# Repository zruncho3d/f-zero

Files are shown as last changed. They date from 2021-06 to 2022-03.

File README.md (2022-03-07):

# F-Zero - an Evolved Voron Zero

by Zruncho and `#flying-zero` collaborators on the [DoomCube Discord](https://discord.gg/doomcube):
L.e.o.p.a.r.d, finn, Kayos Maker, hartk, ericsson, sci, and more.

**Upgrade your V0 or build a fresh F0.**

**Full auto-calibration at a fraction of the price of a V2.**

**Make every first layer perfect!**

### → [See one in action!](https://youtu.be/jLSPeJ7L9R4)  (V0.802 Serial Request)
### → [See CAD in your browser!](https://grabcad.com/library/f-zero-cad-1)
### → [Parts List!](https://docs.google.com/spreadsheets/d/1EkonubBAvg1huz3OgxQa6iyDdansaWyFQbpp1GPkiBE/edit#gid=0): delta relative to V0.1
### → [Get Support!](https://discord.gg/doomcube) (#flying-zero on DoomCube Discord)

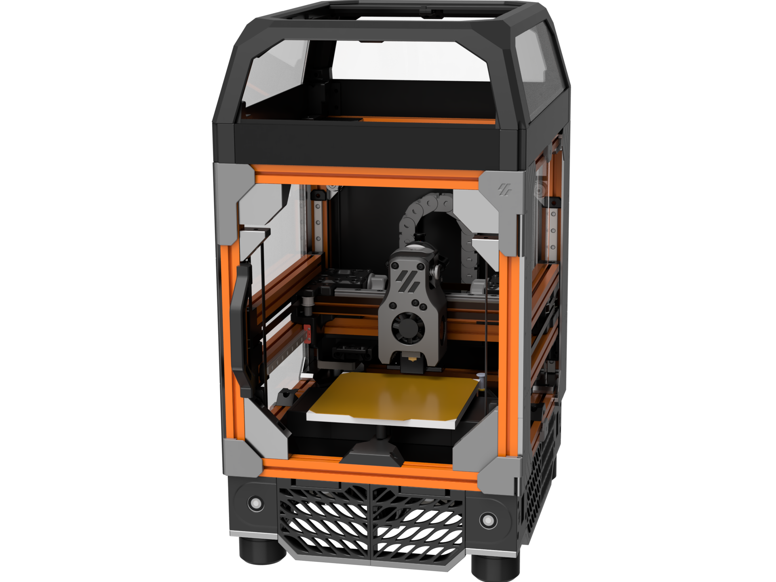
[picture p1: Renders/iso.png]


Join us on the [DoomCube Discord](https://discord.gg/doomcube) for the latest info and any questions.

### Buildlog and Design Doc

[See the Assembly Manual and Buildlog Gdoc](https://docs.google.com/document/d/1dm8itefYrLIsCcOQht9sdMzrXE8Jk30s56c9IwtRCkM/edit#heading=h.c4f5tznx0p31) for more details.

This doc currently has all assembly notes - **definitely check it out if you're considering a build.**

## Goal

**Build a flying-gantry printer using v0 Components.**

**Or put another way**: mod the V0 into a flying-gantry CoreXY printer.

**Why?**  Why not?  Main reason: fun.

* **More fun to build.**
    * It’s a longer but easier build.  Everything is pretty straightforward to put together.  With printed corners, you can remove any single extrusion at any time to add nuts later without huge pain.
* **More fun to run.**
    * Quad Gantry Leveling is a huge Quality-of-life bonus.  No manual bed tramming is needed!
    * Automatic Z Calibration is a nice Quality-of-life bonus.  No work when switching out flexplates of varying height, changing nozzles, or just doing maintenance.
* **More fun to mess with.**
    * This is a fun way to try out new software features and mods, with a faster iteration cycle.  Think of it as a low-cost “V2 trainer” or a fully-evolved V0.  
* **More affordable.**
    * All the features of a V2 at ½ or ⅓ the cost.  ~$200 or less to upgrade a V0.

Other benefits:
* **More-scalable build.**  
    * Untested currently, but 150x150x150 or even 180x180x120 may be doable without huge mods, and this should enable a nice upgrade path for V0s or larger builds.
* **No Z wobble**.
    * Belt drives prevent Z wobble and make for easier sourcing.
* **Reuses much of the V0 ecosystem**
    * Reuses gantry improvements (like MGN9 and dual MGN7 rails), tophat designs, LED mounts, frame kits, toolhead mods… tons of stuff.

### Status Updates

* **2022-03-06**: At least six are printing, or have printed.  Other F0 builds are underway!  All parts + CAD to build your own are available.  Why the lack of major updates?  Because this thing works... that's why.  Everything is out there for you to make your own, and has been for months.

* 2022-02-21: F0.002 is going strong, beyond 350 hrs of printing without a rebuild.  
* 2021-11-24: Updated NEMA17 motor mounts + CAD available now.
* 2021-11-23: Sci fixed an issue with the 2xMGN7 carriage mount.  Thanks!
* 2021-11-20: Side-panel STLs added to GitHub.  Print with concentric infill for extra style.
* 2021-11-15: Congrats Electroleon on getting an F-Zero printing!  Blueberry filament looks awesome.
* 2021-11-02: Fastener list added to BOM.  Tentative total: 533 fasteners (ignores some reused V0 parts though, so lower delta in practice).
* 2021-10-20: Congrats on an awesome printer printing, EG!
* 2021-10-19: BOM moved to GSheet and updated with fastener info.  Not done yet, though.
* **2021-10-17: Full CAD (well, everything but fasteners) added to GitHub.**
* 2021-10-17: New Z joints, with KGLM-03 joints headed to GitHub.  Sources noted below too.
* 2021-10-05: Lots of parts added or moved around in GitHub, including many electronics spacers, the gantry wire organizers, and more.
* 2021-09-25: [Zerofilter](https://github.com/zruncho3d/zerofilter) released!  A filter that fits in the tightest of spaces, including under F-Zero’s bed.  See
* 2021-09-23: [Second serial request]((https://www.reddit.com/r/voroncorexy/comments/ptrhjn/serial_request_v01_fzero_discord_ericsson4763/) and Youtube video is up!  Congrats Ericsson!  Sweet printer with nice customized skirts, mini display, and panels.
* 2021-09-21: [First serial request](https://www.reddit.com/r/voroncorexy/comments/pt235s/serial_request_v01_zruncho1790_fzero_a_flying/) and Youtube videos are up!  \
 [https://www.reddit.com/r/voroncorexy/comments/pt235s/serial_request_v01_zruncho1790_fzero_a_flying/]
* 2021-09-17: Sample Klipper configs will have a mix of Protoloft’s Z-Calibration and Klicky macros.  Full auto-calibration is working nicely now.
* 2021-09-14: See ``#zero-filter` on the DoomCube discord: filter designed
* 2021-09-06: New front skirts designed, which match the rears.  
* 2021-09-06: F-Zero-Orange prints!!!  Also - it’s enclosed, too.
* 2021-08-29: Lots of new parts designed and tested, including a magnetic-attach rear-of-gantry wiring unit and Z chain attachments.  
    * Bottom 1515 attachment for 75%-size Panzer chain
    * Top attachment for 75%-size Panzer chain
    * Simple between-AB-drive box to hide 2 stepper motor connectors + Y endstop and receive the toolhead wires, then send them to the 75%-size Panzer chain
* 2021-08-20: Side skirts fit, and work nicely with existing, unmodified V0 side panels.  They require a bit of printing, but nobody will mistake your printer for anything else.  Top extensions - to the frame, the side panels, and the top panel, to cover all gaps for existing, unmodified V0 side panels - will be added to the GitHub repo soon.
* 2021-08-15: In-progress CAD made available on Discord
* 2021-08-08: Side skirts added.
* **2021-08-02:** Another one prints!  Congrats, ericsson!
* 2021-08-01: Another one QGLs! Congrats, ericsson - your Black Frame / Orange Accent F-Zero is a thing of beauty.  I’m sure printing will come soon.
* 2021-07-27: Gantry attachments updated again on GitHub, to preemptively avoid flex from MGN7 carriages.
* 2021-07-20: Gantry attachments updated on GitHub.
* 2021-07-13: Moving to Klicky for autoprobing.  BOM now up-to-date.  Parts by Kayos, soon.
* 2021-07-11: F-Zero#2 with printed corners is coming to life shortly… stay tuned!
* 2021-07-08: Printable baseplate designed and tested.
* 2021-07-07: Extrusion-oriented bed mount (“space invaders”) designed and tested.
* 2021-07-03: It’s my go-to printer now.  This printer has not had a failed print yet.
* 2021-07-03: Added NEMA17 motor option and bugfix for NEMA14 mounts on GitHub
* **2021-06-26:** First print!  A poker chip, but it’s a start.  Calibration needed, for sure.
* 2021-06-26: Back from some work focus.  Time to validate the toolhead.
* 2021-06-09: Corner joint STLs added to [https://github.com/zruncho3d/f-zero](https://github.com/zruncho3d/f-zero)
* 2021-06-07: STLs released to [https://github.com/zruncho3d/f-zero](https://github.com/zruncho3d/f-zero)  
* 2021-06-04: New Z joints working well for QGL
* 2021-06-01: New Z joints designed, using hobby spherical joints pressed into plastic holders.  Untested but looking good.
* 2021-05-31: First QGL, using Euclid probe!  Not 100% repeatable due to gantry-magnet alignment, but works.
* 2021-05-25: Gearboxes and belt blocks finalized, probe mount added, electronics mounted.  Getting close!
* 2021-05-18: Initial BOM added.
* 2021-05-16: Complete frame built.  See below.
* 2021-05-12: Partially designed, partially built.  See below.
* 2021-05-12: `#flying-zero` on DoomCube Discord added.
* 2021-05-01: Zruncho has Idea for F0, motivated by Hartk’s Micron render, and starts CAD and concepts.
* 2021-04-30: Hartk1213 [shares a render](https://discord.com/channels/460117602945990666/635687829254701107/837819803241545769 ) of what will become Micron on #voronuser_mods

### Parts in this Repo

In this repo are all the STLs you need to make an F-Zero, except for:
- Voron 0.0 or 0.1 parts, including gantry, toolhead, carriage retainers, tophat, and M2 nutbars
- Z endstop (see #micron-v2 on DoomCube Discord)

All parts should be already be in print-ready orientation, and no supports are needed.

Standard Voron settings, or lowered infill and fewer perims, should work fine for most parts:
- 3-4 perimeters
- 16-40% infill, depending on the part
- 0.4-0.5mm width
- 0.2mm layer height

Exceptions include:
- Frame Corners: print at 5 or 6 perimeters, 10% infill, 0.16mm layer height (seriously)
- Electronics Mezzanine Spacers: print at 3 perimeters, 0% infill, 0.2 layer height
- NoDropNuts: print at 3 perimeters, 0% infill, 0.2 layer height

### FAQ

#### Q: F-Zero vs Micron… what’s the difference?

If you're asking this question, you should probably visit the [3D Printers for Ants](https://3dprintersforants.com/) website first, to see a visual landscape of the latest small printers.

To answer your question though... **at a high level, F-Zero and Micron have the same idea:** take the best quality-of-life features from larger printers, and put them on a small printer.

Both have ~120mm-on-a-side build space, use 1515 extrusions, use Klicky and 4 Z motors and belt reduction to enable QGL, have NEMA14-size motors on the gantry, and use the MiniAB from the V0.1 - **but each has a completely opposite execution.**

Hartk took the Voron 2.4 design and scaled it down to create Micron.  It looks like a V2, but smaller.  

Zruncho took the V0 design and wrapped it in a box to create F0.

Micron lives in its own ecosystem, with the V0 toolhead being the only shared item.

F0 lives within the existing V0 ecosystem (the gantry is unchanged!), so you can use existing V0 kits and parts, including LDO color frames, pre-cut panels, toolhead and umbilical boards, and more.  With almost 1500 serial’ed V0s as of March 2022, **this is a huge ecosystem**.  Your wallet gets to benefit from the price competition between suppliers that is only possible with a large ecosystem.  Your printer gets to benefit from the innovative new products that often emerge to support large market: things like easier-to-assemble [visible-joint frames](https://www.aliexpress.com/item/1005003198676826.html), super-solid [metal X-carriages](https://www.aliexpress.com/item/1005003371851612.html), and more.  This attribute is true for any V0-based mod, including [Tri-Zero](https://github.com/zruncho3d/tri-zero), [Double Dragon](https://github.com/zruncho3d/double-dragon), and any others.

**Size?**  From a size perspective, Micron is wider than a V0 or F0 by 20mm, while F0 is deeper by 50mm than both V0 and Micron.  Really, though, they’re both pretty small.  The V0 design is extremely space-efficient in the XY direction, while Micron uses a wider V2-style gantry that removes the need for two extra extrusions.

**Parts?** Nearly all non-printed parts, minus the frame, are shared between the two designs, but nearly all printed parts are different, with the exception of the MiniAB toolhead, which both share with the V0.

**Prints?** Both can print amazingly well and fast, and should scale similarly to larger sizes.

**Documentation?** Micron has its own manual, while F0 has build notes and is able to reuse much of the V0 manual.

**The Takeaway:** If you already have a V0, and want to do an upgrade, F0 is a great option, as it retains more of a V0 kit; you won’t need to waste money on new panels or a new frame, and you'll have fewer parts to print.

It’s more of a personal preference for fresh builds.

#### Q: Can I get a Voron Serial for my printer?

A: Absolutely! The Voron Team is great about supporting heavily modified printers, as long as they carry the essence of the originals (Zruncho’s view, not an official line).  

A successful serial request grants access to Voron Owners Club Discord channels and more: see [the Truth about Voron Owners Club](https://www.reddit.com/r/voroncorexy/comments/q1gk2e/the_truth_about_the_voron_owners_club_voc/).

You can learn a lot from checking out these serial videos and the corresponding reddit discussions:

* [Serial Request - V0.1 zruncho#1790 (F-Zero: a Flying Voron Zero)](https://www.reddit.com/r/voroncorexy/comments/pt235s/serial_request_v01_zruncho1790_fzero_a_flying/)
* [Serial Request V0.1 - F-Zero Discord: ericsson#4763](https://www.reddit.com/r/voroncorexy/comments/ptrhjn/serial_request_v01_fzero_discord_ericsson4763/)

#### Q: Can I just increase the height of the vertical extrusions and skip the printing and sourcing for a tophat?

Absolutely.  Just make sure to increase the height of your panels to go with it.

#### Q: What’s the deal with X carriage options?

V0.1 carriages inform the design of any F-Zero carriages, and you have at least two choices currently, both contributed by Kayos Maker, with the 2xMGN7H option fixed by sci.   

Context, first: on the stock V0.1, a symptom called “toolhead flop” is common, and the root cause is a combination of (1) significant toolhead weight on a long-ish lever arm, at least relative to the rail width, and (2) low-cost MGN7 rails that tend to be loose (low preload).

You can ignore toolhead flop and may still see high-quality prints, especially with the input shaper tuned in Klipper, with accelerations set to low (say, sub-3K) values, and/or with high preload rails (hard to find, $$).  

However, it seems better to reduce the potential for hotend motion to create print artifacts or (F-Zero-specific) probing inaccuracies, and just go with a single larger MGN9C rail or two MGN7 rails.

##### 1xMGN9C

MGN9C rails fit in nearly the same space as MGN7H (only a few mm wider at the carriage, but not longer) and they’re a low-cost, easy way to reduce toolhead flop.  This option has been used on at least FZ.002 with success.

If using this option, ideally you’ll need to create extra space for the slightly-thicker carriage of an MGN9. Either:

* (Preferred, if it clears) Tighten screws with the MGN9 holes offset to get about 0.5mm of Y offset
* Use modified V0 AB blocks with a bit of extra setback, [like these from nchiu](https://github.com/nhchiu/VoronMods/tree/main/V0/X_axis_MGN9C) or [like these (from VoronMods)](https://github.com/VoronMods/V0/tree/main/2nd_X_rail_for_V0.1_mini_AB/)
* Add spacers, such as 2x M3x6 BHCS with spacing nuts in the X gantry extrusion, facing the motor blocks
* Add [printed spacers from the F-Zero repo](https://github.com/zruncho3d/f-zero/blob/main/STLs/Gantry/mgn9_spacer_x2.stl), and mount them with 4x M3x6 BHCS

##### 2xMGN7H on opposite sides

Doubling the MGN7 rails is another option, and it’s known to provide a meaningful reduction in flop, with a few downsides:

* the extra area can potentially block hotend-cooling airflow
* parallel rails require proper alignment
* extra weight from two rails
* you lose ~1 mm of Y travel for the extra space by which the MGN7H carriage sticks out from the extrusion

If the spacing between the carriages is too small, this part will add significant preload to the rails, potentially causing them to bind.  When printing in ABS, the part will shrink (measured by sci and zruncho to reduce from 31mm to ~30.7mm), and this shrinkage needs to be taken account to avoid binding. \
 \
Props to sci on Discord for diagnosing and fixing this problem with [PR #2](https://github.com/zruncho3d/f-zero/pull/2), which adds space between the carriages to reduce the potential for binding.

This option has been used on at least FZ.000 with success, even without added space.

##### 2xMGN7H with orthogonal mount {#2xmgn7h-with-orthogonal-mount}

VoronMods [has a double-X mod](https://github.com/VoronMods/V0/tree/main/2nd_X_rail_for_V0.1_mini_AB), but it would need a carriage update to provide a Klicky mount.

#### Q: What bed space do I lose, relative to a V0?

You’ll lose a tiny bit near the (x=120, y=120) corner due to having an endstop there.  If using an overhanging sexbolt endstop, you’ll lose 0 mm of Y travel.  If using a non-overhanging one, you’ll lose a few MM of Y travel as a result, because the nozzle needs space to press down.

You’ll lose about 1.5mm of Y travel if using the MGN9C option but not using modified AB blocks.

You’ll lose a chunk in the (x=0, y=120) corner due to having the Klicky mount there on all options.

If that’s too much, there’s at least one modded MiniAB which supports an inductive probe, which doesn’t cause any loss of travel.

#### Q: What stuff _don’t_ I need from a V0.1 kit if going straight to a fresh F0 build?

The vast majority of **non-printed** stuff is reused.  Exceptions include:

* bed springs (x3)
* integrated-leadscrew stepper and nut
* various fasteners used for attaching Z-drive components and the frame

The vast majority of **printed** stuff is reused, too.  Exceptions include:

* all Z-drive parts
* skirts
* X carriage mount (needs one with a Klicky mount)

#### Q: Why?  A: Why not?

#### Q: Why not a V1 then?  A: No leadscrew wobble. Auto-calibration. Cost.

#### Q: But isn’t there a belted V0 mod already that ditches leadscrew? A: Yes.

It’s from [thefpvgeek](https://github.com/theFPVgeek/VoronUsers/tree/master/printer_mods/theFPVgeek/v0-zbelt-mod), it’s great, and Zruncho used to use it.  But you still need to manually calibrate.  Z carriage screws are still hidden and a pain to retighten.

#### Q: Can build a larger F0?  A: Yes, with work.

The design should support at least up to 50mm extra travel in each dimension, as a fully boxed frame, printed frame corners, and fully-supported bed yield a printer much more rigid than a regular V0.  An “F-Zero Plus” with +50mm in some or all dimensions would be a great printer.  A +50mm-X, +50mm-Y variant might even use some off-the-shelf beds which provide ~170mm of printable space in each dimension.

You’ll need to do a little bit of work and buy different parts.

If unenclosed:

* Modify baseplate with extra width and length (straightforward in CAD: split, extrude, join)
* Modify rear separator with extra width and length
* Source longer rails
* Source longer extrusions
* Modify or find longer skirts
* Source/build a larger bed and larger heater
    * Need more power if using a DC bed instead of AC w/SSR

If enclosed:

* Modify/use tophat extensions or just use longer Z extrusions and no tophat
* Use larger side panels
* If larger Z, modify side enclosure pieces.

If that’s too much work, consider other Voron-derived/inspired small-printer choices at [www.3dprintersforants.com](www.3dprintersforants.com).  

#### Q: Aren’t lead screws, especially the integrated ones with V0.1, just fine?  A: Yes.

Lead screws are fine.  A stock V0 prints amazingly well.  QGL is a quality-of-life improvement, but by ensuring calibration, is also a quality-of-printing improvement too.

#### Q: Well, what are the downsides?  A: Cost + complexity.

* Cost of additional components: 3x additional motor drivers + board + belts + pulleys + probe switch.
* Additional build time for each Z drive.
* Additional overall complexity and stuff to break.

#### Q: So it’s more expensive, for the same print volume, with greater complexity? A: Yes.

If you’re on a budget and optimizing for print volume or simplicity, there are many other choices for you.

If you like the idea of automatic bed tramming, this may be for you.

#### Q: I want to build one.  How can I learn more?  A: A few ways.

* Go to `#flying-zero` on the [DoomCube Discord](https://discord.gg/doomcube).  Share your idea and progress there!

#### Q: Can I apply the Double Dragon mod to an F-Zero?  A: Yes, with lots of work, and you might regret it.

[Double Dragon](https://github.com/zruncho3d/double-dragon) is a Voron Zero mod to add Independent Dual Extrusion (IDEX) to a V0-size printer (called “X0”).  By default, X0 adds 100mm of width, while F-Zero adds 50mm of depth.

In theory, you could combine these two mods… but:

* You’d have to merge the F0 corner joint design with the X0 Y drive idlers, and this would likely give up Z travel.
* The Y-drive steppers are lower in X0, so they’d smack into the rear baseplate.
* The added weight means you’d need to use beefy motors, probably mid to large-size NEMA17s.
* The baseplate would need to be widened, and any X0 panels deepened.

If you really want X0 with automatic bed leveling, [Tri-Zero](https://github.com/zruncho3d/tri-zero) is probably a better choice, because the extra weight of the longer X rail and additional toolhead is borne by the frame, not a flying gantry.

#### Q: Why do the idlers have formed threads, vs the usual heatsets?  A: Alignment.

The formed thread helps to ensure that the idler stays perfectly parallel to the drive pulley; heatsets enable misalignment, and this is one place you don’t want misalignment causing premature belt wear.

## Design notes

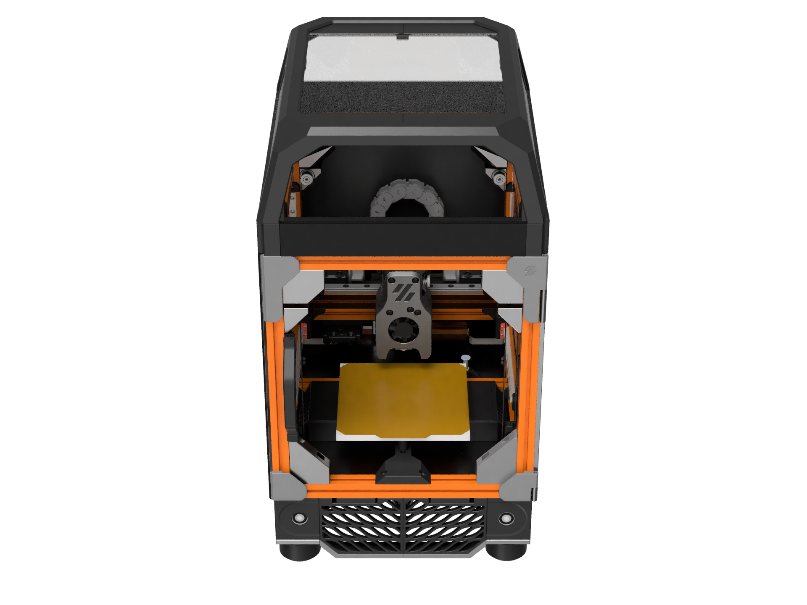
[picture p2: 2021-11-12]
Renders/front_tilted.png

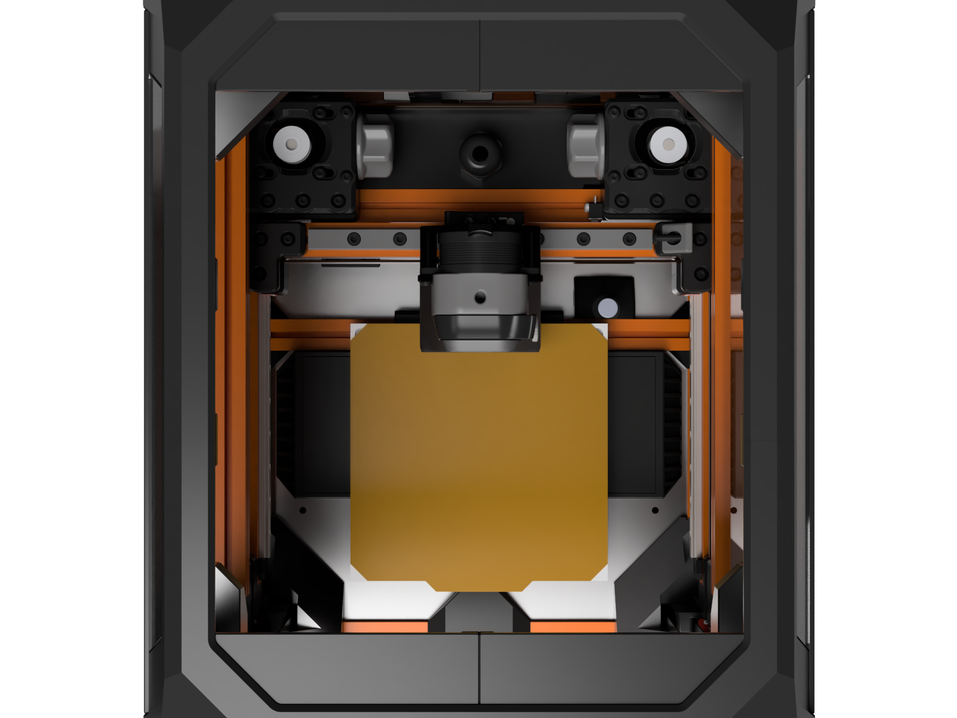
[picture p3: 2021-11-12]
Renders/top.png

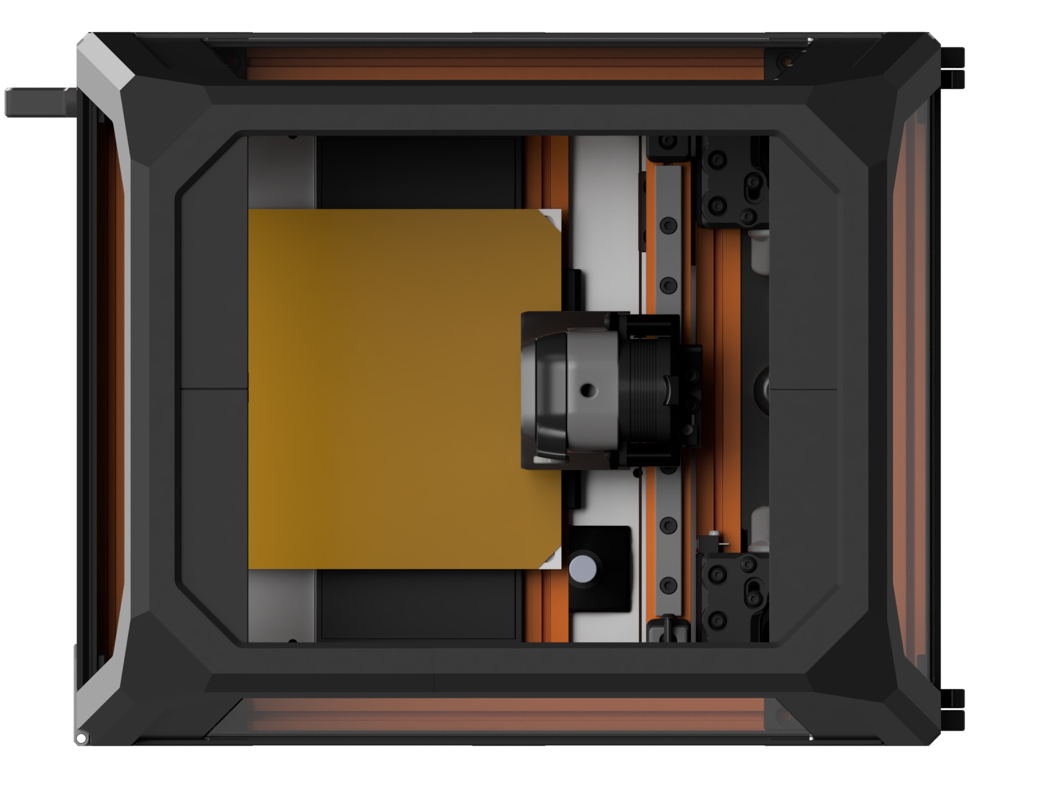
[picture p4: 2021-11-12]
Renders/top_wide.png

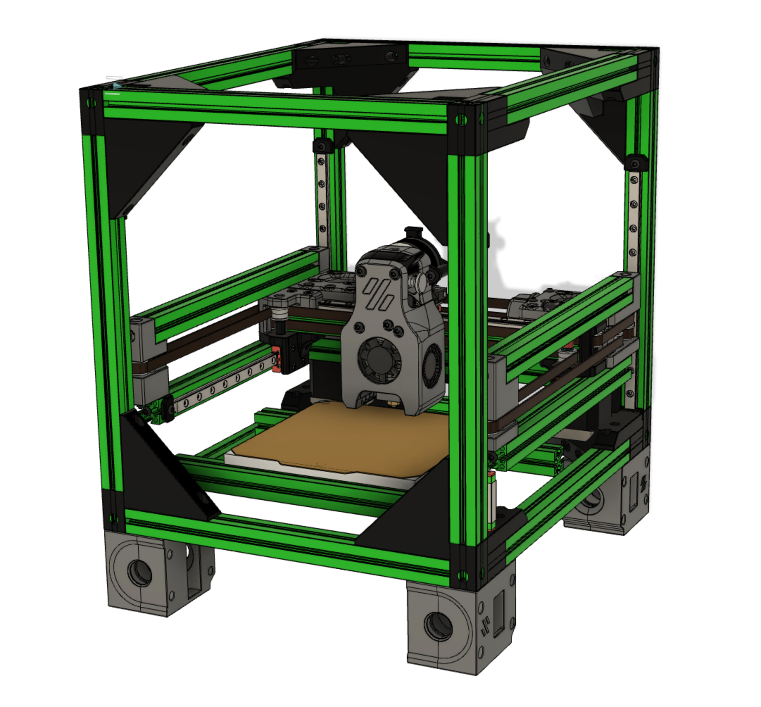
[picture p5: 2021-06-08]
Images/front_green_black_silver.png

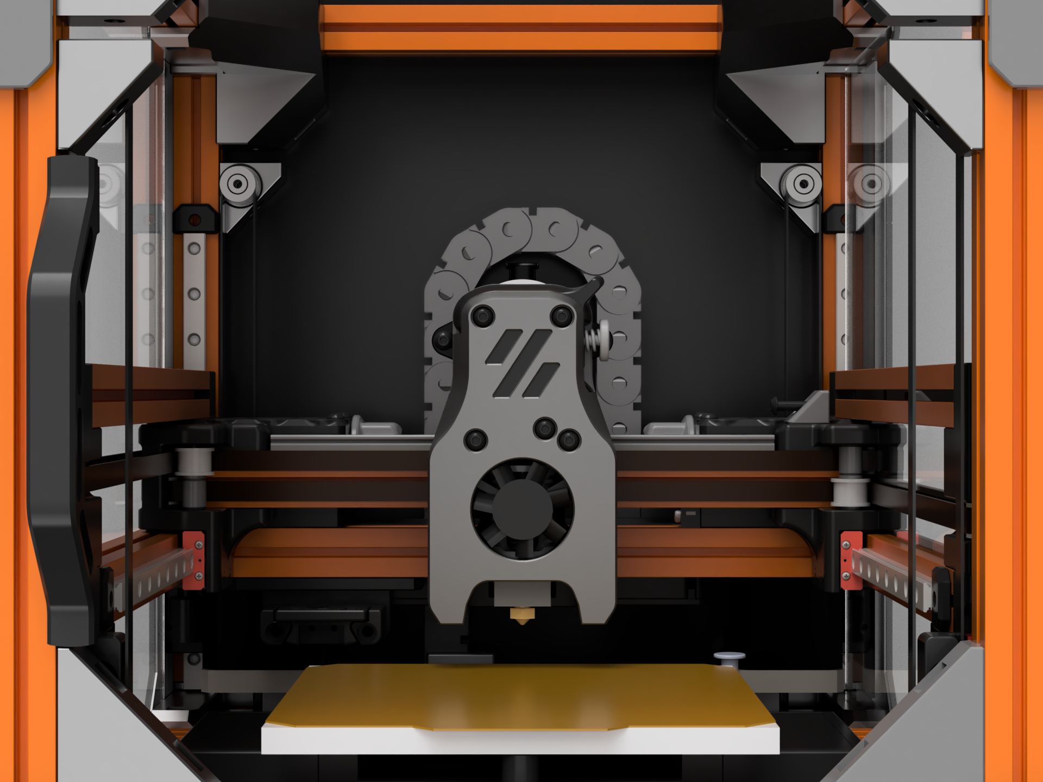
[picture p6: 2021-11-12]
Renders/front_zoomed.png

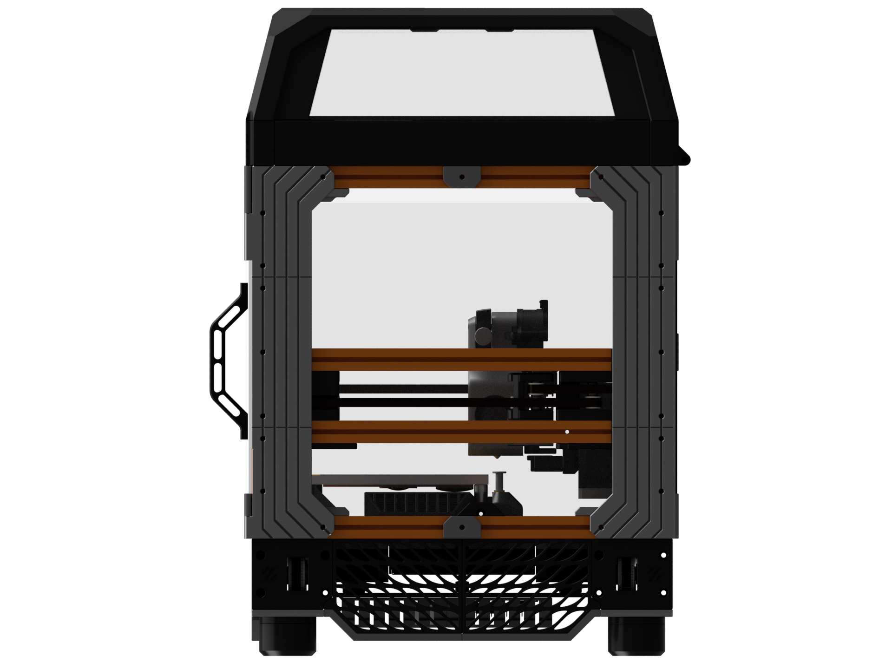
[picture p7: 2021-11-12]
Renders/side.png

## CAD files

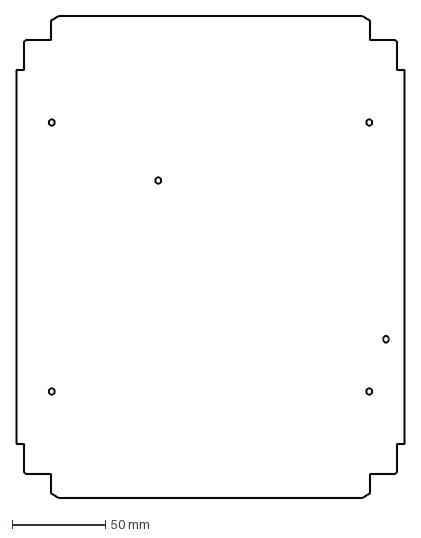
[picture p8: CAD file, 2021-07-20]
baseplate_drawing.dxf
208.0 x 258.0 mm

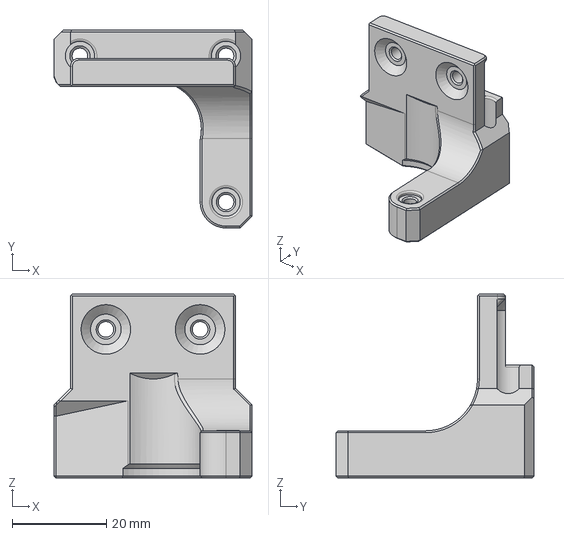
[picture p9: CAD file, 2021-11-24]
CAD/Z Motor Bracket Narrow NEMA17.step
42.0 x 42.0 x 39.0 mm

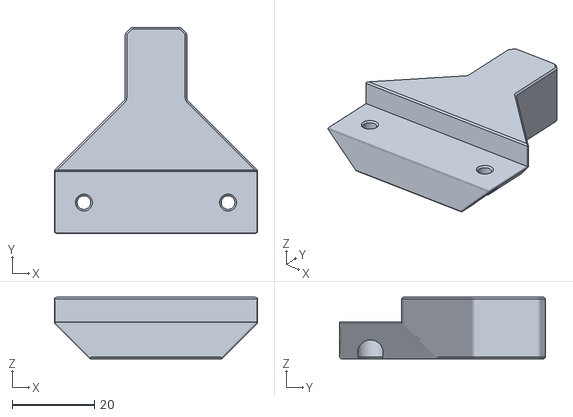
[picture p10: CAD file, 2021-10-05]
STLs/Bed/bed_mount_front_x1.stl
49.3 x 50.0 x 15.0

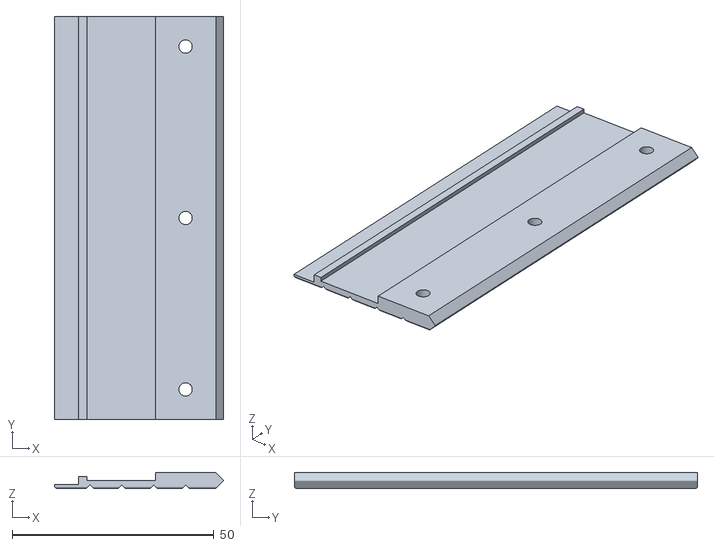
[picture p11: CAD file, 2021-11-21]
STLs/Enclosure/middle_x3.stl
41.9 x 100.0 x 4.00

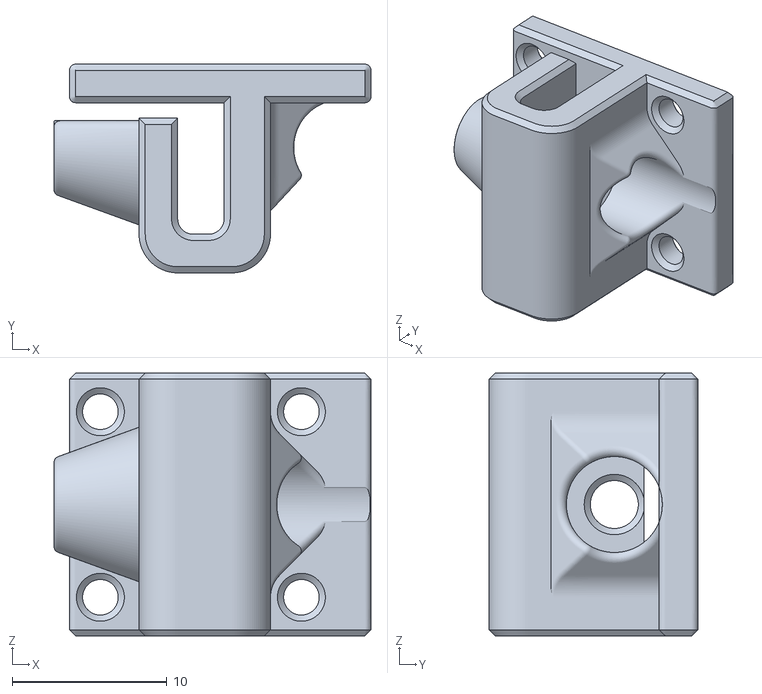
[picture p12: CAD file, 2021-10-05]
STLs/Experimental/experimental_z_joint_carriage_attachment_flexure_style_x4.stl
20.5 x 13.5 x 17.0

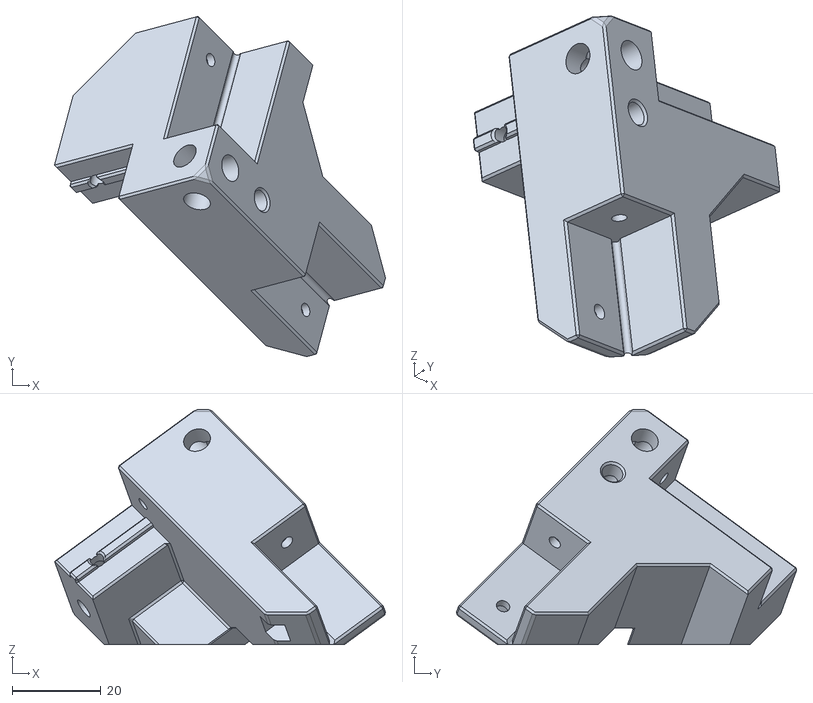
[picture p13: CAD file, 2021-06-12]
STLs/Experimental/Frame_Corners/corner_front_right_top.stl
74.8 x 76.9 x 53.1

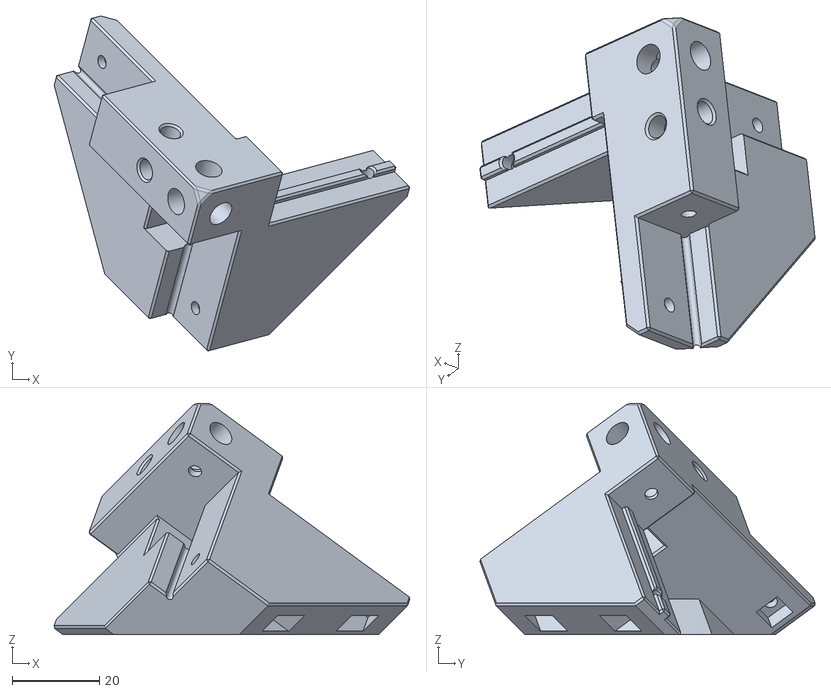
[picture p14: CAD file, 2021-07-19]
STLs/Frame/Frame_Corners/corner_front_left_bottom_24.stl
81.6 x 76.9 x 53.1

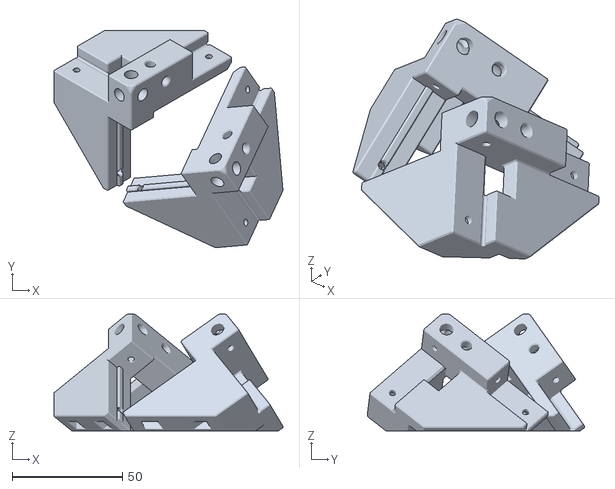
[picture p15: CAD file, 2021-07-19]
STLs/Frame/Frame_Corners/Plates/corner_rear_bottom_24_plate.stl
104.0 x 98.8 x 53.1

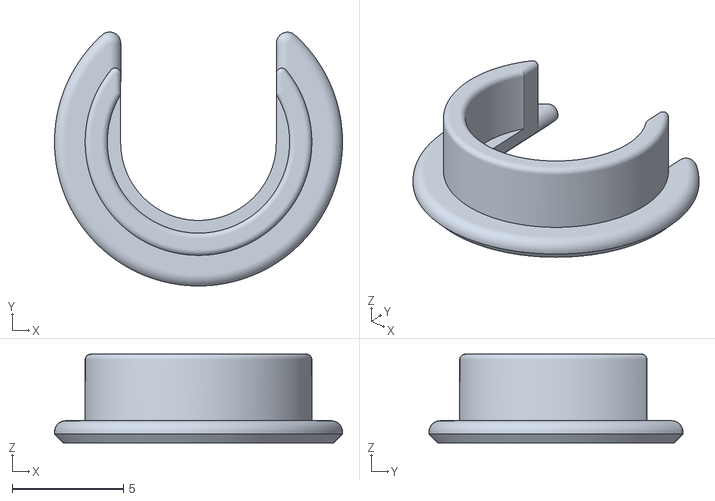
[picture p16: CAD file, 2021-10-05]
STLs/Frame/grommet_inner_x2.stl
13.0 x 11.4 x 4.00

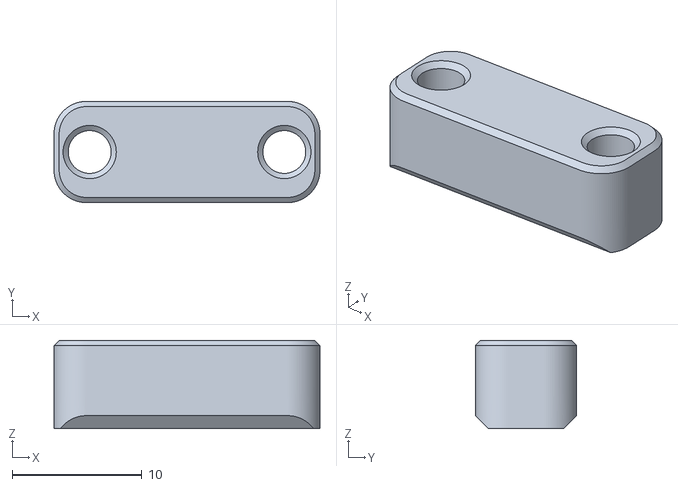
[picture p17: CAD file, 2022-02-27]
STLs/Gantry/adxl_spacer.stl
20.5 x 7.80 x 6.80

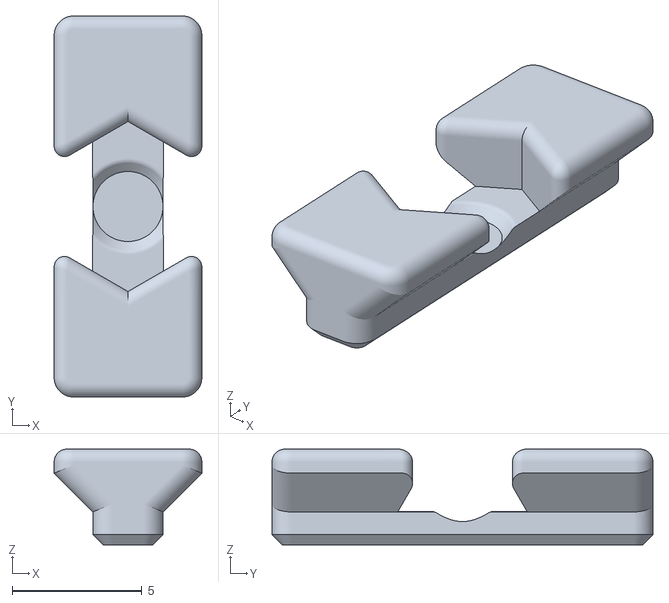
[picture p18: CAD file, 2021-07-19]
STLs/NoDropNuts/NoDropNut_MBXL_LDO_15mm_no_grip.stl
5.70 x 14.7 x 3.70

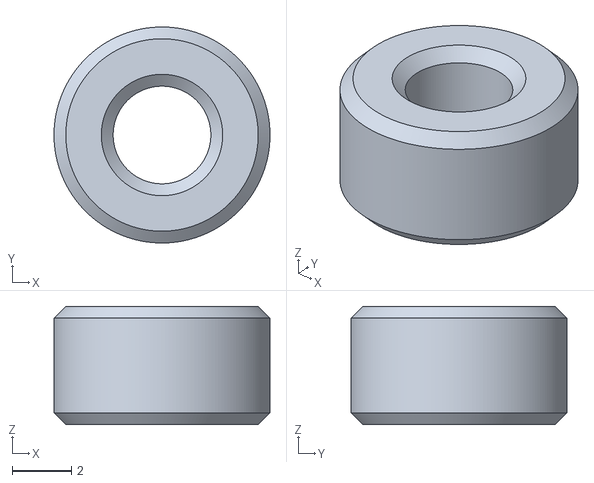
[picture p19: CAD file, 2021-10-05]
STLs/Other/spider_spacer.stl
7.30 x 7.30 x 4.00

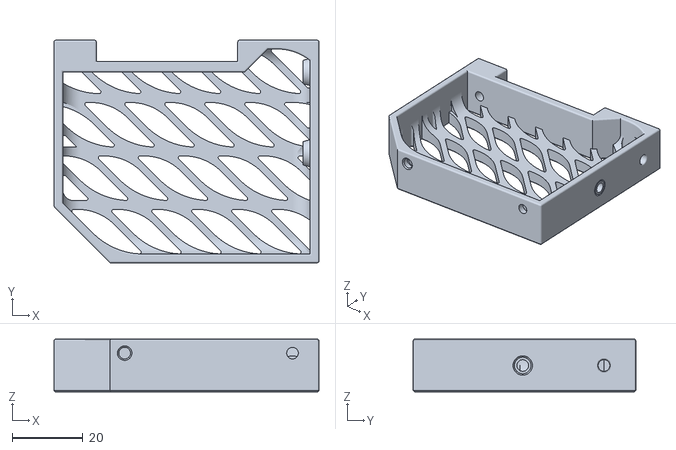
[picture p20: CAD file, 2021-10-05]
STLs/Skirts/front_skirt_mirrored_x1.stl
75.0 x 63.0 x 15.0

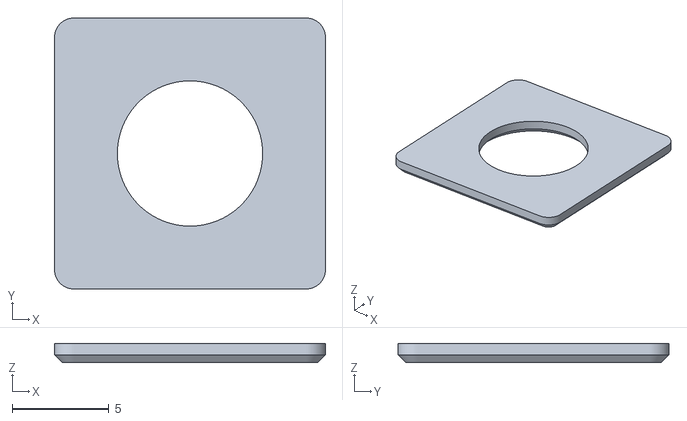
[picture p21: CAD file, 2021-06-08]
STLs/Tools/z_joint_spacer_tool.stl
14.0 x 14.0 x 1.00

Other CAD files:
STLs/Z_Attachments/z_belt_attachment_x4.stl
STLs/Z_Chain/rear_chain_attach_x1.stl
STLs/Z_Drives/z_motor_bracket_nema17_narrow_mirrored_x2.stl
STLs/Z_Idlers/z_idler_mirrored_x2.stl
CAD/DualMGN7Carriage v4.f3d
CAD/Z Motor Bracket Narrow NEMA17.f3d
CAD/Z_Joint_Flexure_Style.f3d
CAD/Z_Joint_Flexure_Style.step
STLs/Archived/Frame_Corners/corner_front_right_bottom.stl
STLs/Archived/Frame_Corners/corner_rear_right_bottom.stl
STLs/Archived/Frame_Corners/corner_rear_right_top.stl
STLs/Archived/idler_end_new_x4.stl
STLs/Archived/z_joint_carriage_attachment_x4.stl
STLs/Archived/z_joint_gantry_attachment_new_x4.stl
STLs/Bed/bed_extrusion_bracket_x3.stl
STLs/Bed/bed_mount_center_x1.stl
STLs/Bed/bed_spacer_12mm_x3.stl
STLs/Bed/bed_spacer_5mm_x1.stl
STLs/Enclosure/bottom_hinge_x1.stl
STLs/Enclosure/corner_mirrored_x3.stl
STLs/Enclosure/corner_x3.stl
STLs/Enclosure/middle_hinge_x1.stl
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

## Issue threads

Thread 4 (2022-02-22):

Move idler base part, which is only useful with all-blind-joints frames, into its own area

zruncho3d, 2022-02-22:
Reported by coilboii on Discord - thanks!

zruncho3d, 2022-02-22:
https://github.com/zruncho3d/f-zero/blob/main/STLs/Z_Idlers/z_idler_base_x4.stl

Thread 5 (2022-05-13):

Fix Z unit screws interfering with with skirts

zruncho3d, 2022-05-13:
Example: https://discord.com/channels/825469421346226226/841961639351812107/974558299334795274

Need to modify the Z units to push screws back, plus add clearance in skirts for existing Z unit prints.

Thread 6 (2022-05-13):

Add countersink to motor mount to-extrusion screws, for skirt clearance

zruncho3d, 2022-05-13:
https://discord.com/channels/825469421346226226/841961639351812107/974575536762421248

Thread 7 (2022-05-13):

Update CAD for latest Z belt attachment (and maybe others)

zruncho3d, 2022-05-13:
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

https://discord.com/channels/825469421346226226/841961639351812107/974617830509125652

eduncan911, 2023-02-06:
I think this one can be closed, as the 3rd version with built in belt looping is in the repo:

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

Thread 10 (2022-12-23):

FZeroTophatSpacer::RearCornerTop alignment socked at wrong position

idonasch, 2022-12-23:
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

The hole is obviously at the wrong position.

**Fix**: RearCornerTop::Sketch13 dimension[d274] should rather be 11.5mm from rear face, not 7.5mm from panel mount.

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

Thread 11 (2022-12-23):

Tophat::Extender heat set insert cavities missing in CAD

idonasch, 2022-12-23:
The extrude feature is suppressed in the history....???

**FIX**: un-suppress the extrude feature for the "Extender" object and change its depth to -4.2mm. Also a 0.4mm chamfer would be advised.

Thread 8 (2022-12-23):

FZeroTophatSpacer Panel M3 inserts missing on other side and have wrong size

idonasch, 2022-12-23:
The "Panel" lacks the holes for the brass inserts on one side. The holes are also too big!

Fix:
- change Model Parameter:Panel:sketch1:Diameter Dimension-2 [d67] from 5.8 to 4.8mm
- Activate Panel and mirror extrude2  on YZ plane

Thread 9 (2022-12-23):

FZeroTophatSpacer Panel  lower lip interferes with 1515 top rails

idonasch, 2022-12-23:
Panel lower lip is superfluous and interferes with 1515 rail, see image
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

Fix: remove it from sketch2. SidePanels have no lip either and  relocating it would require supports while printing.

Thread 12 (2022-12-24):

FZeroTophatSpacer::Panel interferes with TH_Lower_Corner_clip

idonasch, 2022-12-24:
The top lip interferes with the corner clip by 4.1mm
**FIX**:
- In Panel  move the history just before the mirror feature introduced in issue#8 fix (missing inserts in panel).
- Use ::Sketches::Sketch2 to cut off 4.2mm of the panels upper panel lip. Add this feature also to the mirror feature and move history again to the very end.

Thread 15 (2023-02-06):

Missing counter-sunk holes in Nema14 versions of z_motor_bracket_nema14_*

eduncan911, 2023-02-06:
It is a bit related to #5 , because I (and several others in Discord) thought it was the skirts that needed modifying.

https://discord.com/channels/825469421346226226/841961639351812107/974575536762421248

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

So, we... uh, modified our front skirts before we knew the Nema17 mounts had counter-sunk holes!

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

eduncan911, 2023-02-06:
I may rebuild down the road with Nema 17s, as I have a stash of them as well.

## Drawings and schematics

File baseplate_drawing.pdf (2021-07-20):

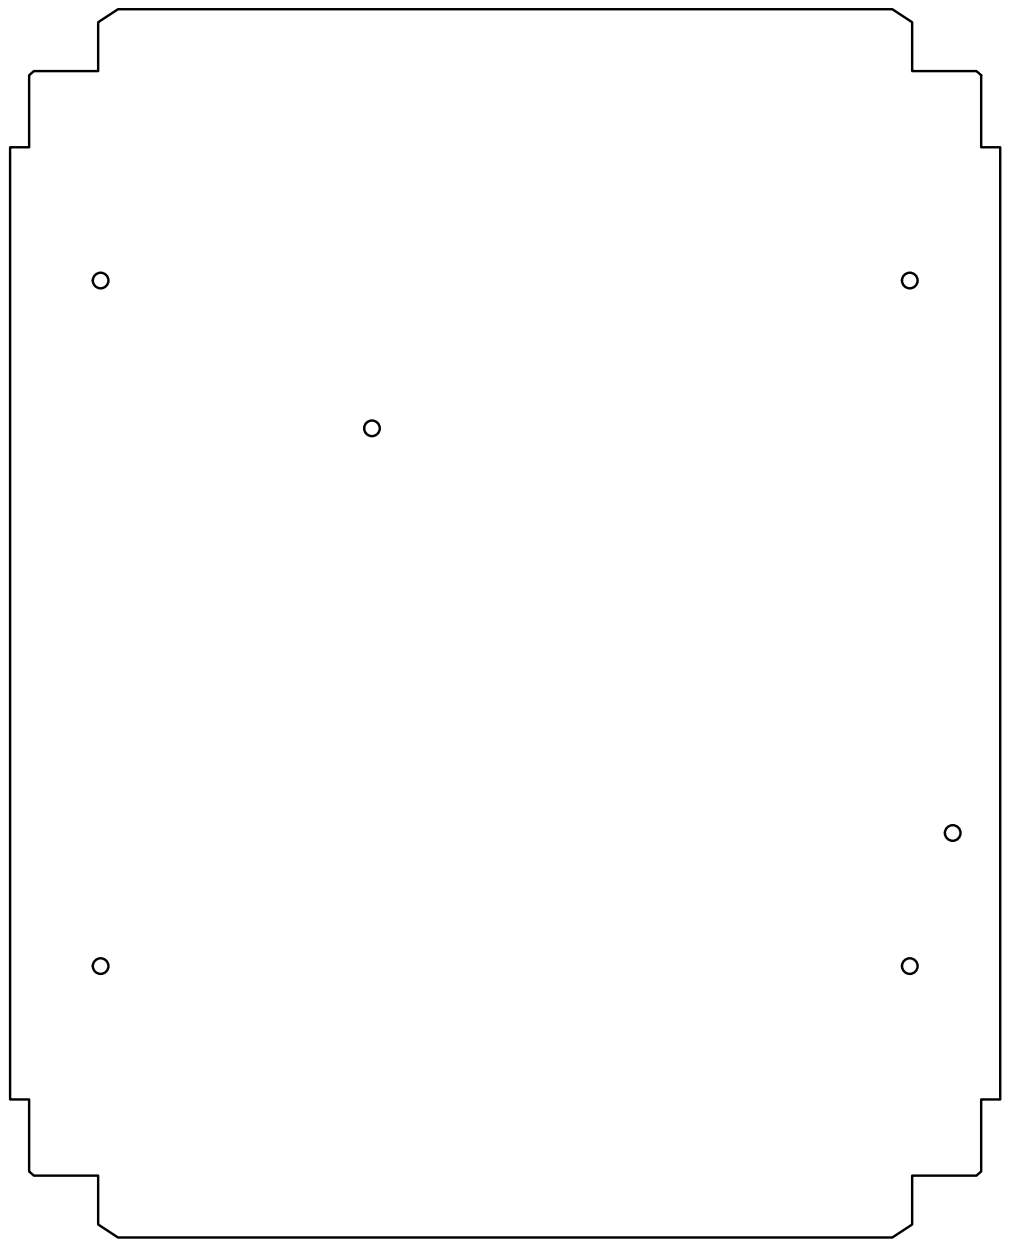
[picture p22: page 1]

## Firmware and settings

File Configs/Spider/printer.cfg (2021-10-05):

## F-Zero Spider TMC2209 UART config, forked from Voron Design VORON2 config

## *** THINGS TO CHANGE/CHECK: ***
## MCU paths				[mcu] section
## Thermistor types			[extruder] and [heater_bed] sections - See 'sensor types' list at end of file
## Z Endstop Switch location		[safe_z_home] section
## Homing end position			[gcode_macro G32] section
## Z Endstop Switch  offset for Z0	[stepper_z] section
## Probe points				[quad_gantry_level] section
## Min & Max gantry corner postions	[quad_gantry_level] section
## PID tune				[extruder] and [heater_bed] sections
## Fine tune E steps			[extruder] section

[include mainsail.cfg]

#[include builtin_extruder.cfg]
[include toolhead.cfg]
[include klicky-probe.cfg]
[include probing.cfg]

[mcu]
##	Obtain definition by "ls -l /dev/serial/by-id/"
##--------------------------------------------------------------------
serial: /dev/serial/by-id/usb-Klipper_stm32f446xx_140017000750305538333620-if00

## Uncomment below if you're using the Raspberry uart0 to communicate with Spider
#restart_method: command

[printer]
kinematics: corexy
max_velocity: 250
max_accel: 3000			        #Max 4000
max_z_velocity: 35			#Max 15 for 12V TMC Drivers, can increase for 24V
max_z_accel: 100
square_corner_velocity: 5.0

#####################################################################
#      X/Y Stepper Settings
#####################################################################

[stepper_x]
##	Connected to X-MOT (B Motor)
step_pin: PE11
dir_pin: !PE10
enable_pin: !PE9
rotation_distance: 40
microsteps: 16
full_steps_per_rotation:200  #set to 400 for 0.9 degree stepper

# If not using a toolhead, uncomment this line.
#endstop_pin: ^PB14

# As of mid-August 2021, Klipper's master branch includes muti-MCU homing.
# See this thread for the Pull Request: https://github.com/KevinOConnor/klipper/pull/3956
# So feel free to put that X endstop on the toolhead!
# Just make sure to modify the config to actually reference it,
# by adding this line in the [stepper_x] section in the main file.
endstop_pin: head0:PA1  #"ENDSTOP", active low

position_min: 0

##  For F0 build
position_endstop: 118.5  ; was 117.5
position_max: 119  ; was 118.5


##--------------------------------------------------------------------
homing_speed: 50   #Max 100
homing_retract_dist: 5
homing_positive_dir: true

##	Make sure to update below for your relevant driver (2208 or 2209)
[tmc2209 stepper_x]
uart_pin: PE7
interpolate: True
run_current: 0.65
hold_current: 0.5
sense_resistor: 0.110
stealthchop_threshold: 500

# .55 / .5 NOT ENOUGH!

[stepper_y]
##	Connected to Y-MOT (A Motor)
step_pin: PD8
dir_pin: !PB12
enable_pin: !PD9
rotation_distance: 40
microsteps: 16
full_steps_per_rotation:200  #set to 400 for 0.9 degree stepper
endstop_pin: ^PB13
position_min: 0

##  For F0 build
position_endstop: 119
position_max: 119.5

homing_speed: 50  #Max 100
homing_retract_dist: 5
homing_positive_dir: true

##	Make sure to update below for your relevant driver (2208 or 2209)
[tmc2209 stepper_y]
uart_pin: PE15
interpolate: True
run_current: 0.65
hold_current: 0.5
sense_resistor: 0.110
stealthchop_threshold: 500

#####################################################################
#   Z Stepper Settings
#####################################################################

## In Z-MOT Position
## Z0 Stepper - Front Left
[stepper_z]
step_pin: PD14
dir_pin: PD13
enable_pin: !PD15
rotation_distance: 32
gear_ratio: 64:16
microsteps: 16
##  In Z- Position
endstop_pin: ^PA0
##  Z-position of nozzle (in mm) to z-endstop trigger point relative to print surface (Z0)
##  (+) value = endstop above Z0, (-) value = endstop below
##	Increasing position_endstop brings nozzle closer to the bed
##  After you run Z_ENDSTOP_CALIBRATE, position_endstop will be stored at the very end of your config
position_endstop: 1.993513

##  For F0 build
position_max: 110

##--------------------------------------------------------------------
position_min: -5
homing_speed: 8
second_homing_speed: 3
homing_retract_dist: 3

##	Make sure to update below for your relevant driver (2208 or 2209)
[tmc2209 stepper_z]
uart_pin: PD10
uart_address: 0
interpolate: True
run_current: 0.8
hold_current: 0.8
sense_resistor: 0.110
stealthchop_threshold: 500

##	In E1-MOT Position
##	Z1 Stepper - Rear Left
[stepper_z1]
step_pin: PE6
dir_pin: !PC13
enable_pin: !PE5
rotation_distance: 32
gear_ratio: 64:16
microsteps: 16

##	Make sure to update below for your relevant driver (2208 or 2209)
[tmc2209 stepper_z1]
uart_pin: PC14
interpolate: True
run_current: 0.8
hold_current: 0.8
sense_resistor: 0.110
stealthchop_threshold: 500

##	In E2-MOT Position
##	Z2 Stepper - Rear Right
[stepper_z2]
step_pin: PE2
dir_pin: PE4
enable_pin: !PE3
rotation_distance: 32
gear_ratio: 64:16
microsteps: 16

##	Make sure to update below for your relevant driver (2208 or 2209)
[tmc2209 stepper_z2]
uart_pin: PC15
interpolate: true
run_current: 0.8
hold_current: 0.8
sense_resistor: 0.110
stealthchop_threshold: 500

##	In E3-MOT Position
##	Z3 Stepper - Front Right
[stepper_z3]
step_pin: PD12
dir_pin: !PC4
enable_pin: !PE8
rotation_distance: 32
gear_ratio: 64:16
microsteps: 16

[tmc2209 stepper_z3]
uart_pin: PA15
interpolate: true
run_current: 0.8
hold_current: 0.8
sense_resistor: 0.110
stealthchop_threshold: 500

# Extruder content moved to builtin_extruder.cfg

#####################################################################
#   Bed Heater
#####################################################################
[heater_bed]
##	SSR Pin - In BED OUT position
#heater_pin: PB4
heater_pin: PA3
sensor_type: NTC 100K MGB18-104F39050L32
# https://keenovo.store/products/keenovo-square-silicone-heater-3d-printer-build-plate-heatbed-heating-pad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
sensor_pin: PC3
##	Adjust Max Power so your heater doesn't warp your bed
max_power: 1.0
min_temp: 0
max_temp: 120
control: pid
pid_kp: 58.437
pid_ki: 2.347
pid_kd: 363.769

#####################################################################
#	Fan Control
#####################################################################

[heater_fan zerofilter_1]
# FAN0
pin: PB0
heater: heater_bed
heater_temp: 40
fan_speed: 0.6

[heater_fan zerofilter_2]
# FAN1
pin: PB1
heater: heater_bed
heater_temp: 40
fan_speed: 0.6

[heater_fan spider_cooling]
# FAN2
pin: PB2
heater: heater_bed
heater_temp: 40
fan_speed: 0.5

#####################################################################
#	LED Control
#####################################################################

#[output_pin caselight ]
##  Chamber Lighting - In E1 OUT Position
#pin: PC8
#pwm: true
#shutdown_value: 0
#cycle_time: 0.01

#####################################################################
#	Homing and Gantry Adjustment Routines
#####################################################################

[idle_timeout]
timeout: 1800

#####################################################################
#	Displays
#####################################################################

#--------------------------------------------------------------------

# [display]
# #	mini12864 LCD Display
# lcd_type: uc1701
# cs_pin: PC11
# a0_pin: PD2
# rst_pin: PC10
# encoder_pins: ^PC6,^PC7
# click_pin: ^!PA8
# contrast: 63
# #spi_bus: spi1
# spi_software_mosi_pin: PA7
# spi_software_miso_pin: PA6
# spi_software_sclk_pin: PA5

# [neopixel fysetc_mini12864]
# #	To control Neopixel RGB in mini12864 display
# pin: PC12
# chain_count: 3
# chain_count: 60
# initial_RED: 0.1
# initial_GREEN: 0.5
# initial_BLUE: 0.0
# color_order: RGB

# #	Set RGB values on boot up for each Neopixel.
# #	Index 1 = display, Index 2 and 3 = Knob
# [delayed_gcode setdisplayneopixel]
# initial_duration: 1
# gcode:
#         SET_LED LED=fysetc_mini12864 RED=1 GREEN=1 BLUE=1 INDEX=1 TRANSMIT=0
#         SET_LED LED=fysetc_mini12864 RED=1 GREEN=0 BLUE=0 INDEX=2 TRANSMIT=0
#         SET_LED LED=fysetc_mini12864 RED=1 GREEN=0 BLUE=0 INDEX=3

#--------------------------------------------------------------------

# From https://docs.mainsail.xyz/quicktips/additional-sensors#raspberry-pi-temperature-sensor
[temperature_sensor raspberry_pi]
sensor_type: temperature_host
min_temp: 10
max_temp: 100

#####################################################################
#	Macros
#####################################################################

[gcode_macro G32]
gcode:
    BED_MESH_CLEAR
    G28
    QUAD_GANTRY_LEVEL
    G28
    ##	Uncomment for for your size printer:
    #--------------------------------------------------------------------
    ##	Uncomment for 250mm build
    #G0 X125 Y125 Z30 F3600

    ##	Uncomment for 300 build
    #G0 X150 Y150 Z30 F3600

    ##	Uncomment for 350mm build
    #G0 X175 Y175 Z30 F3600
    #--------------------------------------------------------------------

    # For F-Zero
    G0 X60 Y60 Z30 F3600
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

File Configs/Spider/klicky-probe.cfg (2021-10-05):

# This macro was provided by discord user Garrettwp to whom i give my thanks for sharing it with me.
# I have tweaked it a lot.
#
# this macro is  based on the great Annex magprobe dockable probe macros "#Originally developed by Mental, modified for better use on K-series printers by RyanG and Trails"
# that macro can be found here https://github.com/Annex-Engineering/Annex-Engineering_Other_Printer_Mods/blob/master/All_Printers/Microswitch_Probe/Klipper_Macros/dockable_probe_macros.cfg
#
# by standing on the shoulders of giants, lets see if we can see further

[gcode_macro User_Variables]
variable_verbose:               True  # Enable verbose output
variable_travel_speed:          200   # how fast all other travel moves will be performed when running these macros
variable_dock_speed:            50    # how fast should the toolhead move when docking the probe for the final movement
variable_release_speed:         100    # how fast should the toolhead move to release the hold of the magnets after docking
variable_z_drop_speed:          20    # how fast the z will lower when moving to the z location to clear the probe
variable_home_z_height:         15    # Z when homing

# if a separate Z endstop switch is in
# use, specify the coordinates of the switch here (Voron).
# Set to 0 to have the probe move to center of bed
variable_z_endstop_x:           118.5
variable_z_endstop_y:           119
#variable_z_endstop_x:          0
#variable_z_endstop_y:          0

# location to park the toolhead
variable_park_toolhead:         False  # Enable toolhead parking
variable_parkposition_x:        150
variable_parkposition_y:        150
variable_parkposition_z:        30

#dock location
variable_docklocation_x:        0    # X Dock position
variable_docklocation_y:        119   # Y Dock position
variable_docklocation_z:        15    # Z dock position
variable_dockarmslenght:        30    # Dock arms lenght, toolhead movement necessary to clear the dock arms

#Umbilical to help untangle the umbilical in difficult situations
variable_umbilical_x:           15    #X umbilical position
variable_umbilical_y:           15    #Y umbilical position
variable_umbilical:             False #should we untabgle the umbilical

# Do not modify below
gcode:
    {% set Mx = printer['configfile'].config["stepper_x"]["position_max"]|float %}
    {% set My = printer['configfile'].config["stepper_y"]["position_max"]|float %}
    {% set Ox = printer['configfile'].config["probe"]["x_offset"]|float %}
    {% set Oy = printer['configfile'].config["probe"]["y_offset"]|float %}
    {% set Oz = printer['configfile'].config["probe"]["z_offset"]|float %}

    # if docklocation_z is zero, use Home Z height for safety
    {% if docklocation_z == 0 %}
        SET_GCODE_VARIABLE MACRO=Probe_Variables VARIABLE=docklocation_z VALUE={ home_z_height }
    {% endif %}

    # If x, y coordinates are set for z endstop, assign them
    {% if z_endstop_x != 0 or z_endstop_y != 0 %}
        SET_GCODE_VARIABLE MACRO=Probe_Variables VARIABLE=z_endstop_x VALUE={ z_endstop_x }
        SET_GCODE_VARIABLE MACRO=Probe_Variables VARIABLE=z_endstop_y VALUE={ z_endstop_y }

    # if no x, y coordinates for z endstop, assume probe is endstop and move toolhead to center of bed
    {% else %}
        SET_GCODE_VARIABLE MACRO=Probe_Variables VARIABLE=z_endstop_x VALUE={ (Mx * 0.5) - Ox }
        SET_GCODE_VARIABLE MACRO=Probe_Variables VARIABLE=z_endstop_y VALUE={ (My * 0.5) - Oy }
    {% endif %}


[gcode_macro Probe_Variables]
variable_probe_attached:            False
variable_probe_state:               False
variable_probe_lock:                False
variable_z_endstop_x:               0
variable_z_endstop_y:               0
gcode:


[gcode_macro Homing_Variables]
default_parameter_reset:            0
gcode:
    {% set R  = params.RESET %}

    {% if R %}
        SET_GCODE_VARIABLE MACRO=Probe_Variables VARIABLE=probe_lock VALUE={ False }
   {% endif %}

# Attach probe and lock it
[gcode_macro Attach_Probe_Lock]
gcode:
    Attach_Probe
    SET_GCODE_VARIABLE MACRO=Probe_Variables VARIABLE=probe_lock VALUE={ True }


# Dock probe and lock it
[gcode_macro Dock_Probe_Unlock]
gcode:
    SET_GCODE_VARIABLE MACRO=Probe_Variables VARIABLE=probe_lock VALUE={ False }
    Dock_Probe

# Unlock Probe
[gcode_macro Probe_Unlock]
gcode:
    SET_GCODE_VARIABLE MACRO=Probe_Variables VARIABLE=probe_lock VALUE={ False }

# Lock Probe
[gcode_macro Probe_Lock]
gcode:
    SET_GCODE_VARIABLE MACRO=Probe_Variables VARIABLE=probe_lock VALUE={ True }
# Attach Probe Routine
[gcode_macro Attach_Probe]
gcode:
    # Get probe attach status
    {% set P = printer["gcode_macro Probe_Variables"].probe_attached %}
    {% set L = printer["gcode_macro Probe_Variables"].probe_lock %}
    {% set V = printer["gcode_macro User_Variables"].verbose %}
    # Get Docking location
    {% set Dx = printer["gcode_macro User_Variables"].docklocation_x %}
    {% set Dy = printer["gcode_macro User_Variables"].docklocation_y %}
    {% set Dz = printer["gcode_macro User_Variables"].docklocation_z %}
    {% set Da = printer["gcode_macro User_Variables"].dockarmslenght %}
    # Safe Z for travel
    {% set Hzh = printer["gcode_macro User_Variables"].home_z_height|float %}
    #Set speed
    {% set St = printer["gcode_macro User_Variables"].travel_speed * 60    %}

    #prior to saving actual position, check if its necessary to move to a safe Z
    #that has enought overhead for the attached probe
    {% if (printer.toolhead.position.z < Hzh) %}
        G1 Z{Hzh} F1200
    {% endif %}
    M400 # mandatory to save the new safe position
    #allows the docking position to be independent of the Z offset, necessary for bed mounted probes
    SAVE_GCODE_STATE name=_attachProbe
    SET_GCODE_OFFSET Z=0

    # if x and y are not homed
    {% if not 'xy' in printer.toolhead.homed_axes %}
        { action_raise_error("Must Home X and Y Axis First!") }

    # If probe not attached and locked
    {% elif not P and not L %}
        {% if V %}
            { action_respond_info("Attaching Probe") }
        {% endif %}
        G90

        {% if (not 'z' in printer.toolhead.homed_axes) %}
            {% if V %}
                { action_respond_info("Resetting Z position to zero") }
            {% endif %}
            SET_KINEMATIC_POSITION Z=0
        {% endif %}

        {% if (printer.toolhead.position.z < Hzh) %}
            G1 Z{Hzh} F1200
        {% endif %}

        Umbilical_Path

        # Probe entry location
        G1 X{Dx} Y{Dy|int - Da|int} Z{Hzh} F{St}
        #lower to Z dock
        G1 Z{Dz} F600
        # pickup from Probe location
        G1 X{Dx} Y{Dy} F1800
        # Probe entry location
        G1 X{Dx} Y{Dy|int - Da|int} F6000
        #Go to Z safe distance
        G1 Z{Hzh} F600
        Park_Toolhead

        CheckProbe action=attach

    {% elif L %}
        {% if V %}
            { action_respond_info("Probe locked!") }
        {% endif %}

        # Probe attached, do nothing
        CheckProbe action=query

    {% else %}
        {% if V %}
            { action_respond_info("Probe already attached!") }
        {% endif %}

        # Probe attached, do nothing
        CheckProbe action=query

    {% endif %}
    #reverts to the original Z offset
    RESTORE_GCODE_STATE name=_attachProbe
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

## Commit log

2021-06-12 Add experimental frame corners
    You'll need to mirror them in your slicer to print the other half.
    [corner_front_right_bottom.stl, corner_front_right_top.stl, corner_rear_right_bottom.stl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]
2021-07-04 Add NEMA17 motor mount option + fix bug on NEMA14 one
    The new NEMA17 option is just like the 14, just chonkier.
    If you got it, use it.
    Also fix a bug with the original NEMA14 mount where the extrusion-
    attachment hole was 1mm off, which meant that the mount would not sit
    flat against the extrusion.
    [z_motor_bracket_nema14_mirrored_x2.stl, z_motor_bracket_nema14_x2.stl, z_motor_bracket_nema17_mirrored_x2.stl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]
2021-07-17 Add parts for new T-shaped bed mount
    This design reuses the 100mm extrusions from a V0 kit, in a T shape.
    Tested; seems good.
    Also added longer bed spacers for bed mounting.
    [bed_extrusion_bracket_x3.stl, bed_mount_center_x1.stl, bed_spacer_12mm_x3.stl]
2021-07-19 Add NoDropNuts (now LDO and MBXL-compatible)
    These are designed to stay in place and only be moved with an a small
    allen wrench gripping on the nut or the (optional) handle.
    [NoDropNut_MBXL_LDO_15mm_grip.stl, NoDropNut_MBXL_LDO_15mm_no_grip.stl]
2021-07-19 Add printable baseplate
    Includes built-in holes for an LRS-100-24 power supply plus 4 holes for
    mounting an electroncis mezzanine.
    Baseplate outer dims are known-good (tested by Zruncho) but the holes for
    the LRS-100-24 are unknown.
    [baseplate.stl]
2021-07-19 Add updated frame corners with different height
    See README.md for more details.
    Also add pre-oriented 2-corner plates for easier printing on a V0.
    [corner_front_bottom_24_plate.stl, corner_front_left_bottom_24.stl, corner_front_left_top_24.stl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]
2021-07-19 Add Electronics Mezzanine Spacers
    I like these. They fit up to 12 zipties apiece and should help
    wrange the wires. Use the one whose height matches your motors:
    NEMA14: 35mm
    NEMA17: 42mm
    Atop them goes a plate for mounting the control electronics.
    You can even reuse a V0 base-panel; it fits perfects between the Z
    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
    [electronics_mezzanine_spacer_35mm_x4.stl, electronics_mezzanine_spacer_42mm_x4.stl]
2021-07-19 Add pulley spacer for using 64t Jetpack pulleys
    [64t_pulley_spacer.stl]
2021-07-19 Add note about printing NoDropNuts
2021-07-20 Add baseplate dxf + stl
    [baseplate.stl, baseplate_drawing.dxf]
2021-07-21 Redesign Z joints and rename tools
    Pointed out by Kayos Maker and totally an issue:
    The current design has one screw in contact with the gantry idler
    assembly. This could lead to losing tension in the gantry if you
    didn't crank down on the screws, OR if creep over time loosens the
    screws to where their positions changes.
    This design fixes that issue and also frees up an extra 3 mm of
    potential Z motion, however it DOES require the new corners, which
    have a 24mm offset.
    [idler_end_x4.stl, z_joint_carriage_attachment_direct_x4.stl, z_joint_carriage_attachment_x4.stl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]
2021-07-27 Update gantry attachments again
    Look for 2 new parts marked with _new,
    which should work with all released corners.
    This is the 4th complete redesign, and hopefully the last!
    Should ensure that the idler is rigidly held and never gets loose, even
    if the plastic creeps slightly and loosens the screw's grip on the
    extrusion under tension.
    Note also: the originally-released z_joint_carriage_attachment file is
    back; it has not been changed.
    [idler_end_new_x4.stl, idler_end_x4.stl, z_joint_carriage_attachment_direct_x4.stl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]
2021-08-07 Add spacer to match MGN9 mod
    [mgn9_spacer.stl]
2021-08-07 Add printed cable channel
    [cable_channel_base.stl, cable_channel_cover.stl]
2021-08-09 Update Z attachment to provide clearance for side panel
    [z_joint_carriage_attachment_x4.stl]
2021-08-09 Update bed mount with 10mm extra
    Tested by ericsson; thanks!
    [bed_mount_center_x1.stl]
2021-08-09 Add new flying-zero side skirts
    Get it? Get it?
    [lower_trim.stl, lower_trim_mirrored.stl, side_skirt.stl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]
2021-08-09 Add Z drive spacer to lift the printer
    [z_drive_spacer.stl]
2021-08-16 Update README.md
    Small tweak to printing instructions
2021-09-05 Update bed mount: smaller & faster-to-print
    [bed_mount_center_x1.stl]
2021-09-18 Add script to analyze bed mesh quality
2021-10-04 Update README.md
    Note printed corner infill
2021-10-05 Add missing STLs used in F-Zero-Orange build
    Also do a few moves for clarity and delete a few irrelevant parts.
    [64t_pulley_spacer.stl, bed_mount_front_x1.stl, euclid_mount_x1.stl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]
2021-10-05 Add known-good Spider sample
    [builtin_extruder.cfg, klicky-probe.cfg, mainsail.cfg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]
2021-10-05 Reorient gantry wire organizer parts for V0 printing
    [gantry_wire_organizer_lid_x1.stl, gantry_wire_organizer_x1.stl]
2021-10-18 Add new KGLM-03 joints
    Many thanks to @sci on the DoomCube discord for help refining this!
    This part is a standard one, vs the random ball joint previously used.
    These parts have been printed and tested over multiple iterations, but have
    not yet been used to QGL or print. I have no doubt they'll be just fine,
    though.
    [idler_end_kglm03_x4.stl, z_joint_carriage_attachment_kglm03_x4.stl, z_joint_gantry_attachment_kglm03_thick_x4.stl]
2021-10-18 Archive prior Z attachment parts
    [idler_end_new_x4.stl, z_joint_carriage_attachment_x4.stl, z_joint_gantry_attachment_new_x4.stl]
2021-10-18 Add CAD
    Includes most everything, except hardware.
2021-10-20 Update Z belt attachments
    Adjusted height for an m8 screw to go through fully, to provide added rigidity.
    [z_belt_attachment_x4.stl]
2021-11-12 Add CAD for experimental flexure style joints
    You're welcome, hartk.
    [Z_Joint_Flexure_Style.f3d, Z_Joint_Flexure_Style.step]
2021-11-21 Add enclosure parts
    All are oriented so that seams are hidden, once assembled.
    [bottom_hinge_x1.stl, corner_mirrored_x3.stl, corner_x3.stl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]
2021-11-24 Add dual MGN7 X Carriage
    Add dual MGN7 X Carriage
    Carriage has been widened by about 0.8% to account for ABS shrinkage, and 1mm has been shaved off of the bottom protrusion so as to reduce Y loss.
    [DualMGN7Carriage v4.f3d, dual_mgn7_x_carriage_x1.stl]
2021-11-24 Add CAD for NEMA17 motor mounts
    Also update STLs to provide clearance for motor-mount-to-extrusion screws,
    to remove the interference with the front skirts.
    [Z Motor Bracket Narrow NEMA17.f3d, Z Motor Bracket Narrow NEMA17.step, z_motor_bracket_nema17_narrow_mirrored_x2.stl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]
2022-02-27 Add ADXL spacer
    [adxl_spacer.stl]
